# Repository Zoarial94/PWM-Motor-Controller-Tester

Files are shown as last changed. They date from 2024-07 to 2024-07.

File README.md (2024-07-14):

This is a board I designed and put together during my time as a mentor on the FRC team 4467 Titanium Titans. The original purpose of this device was to easily test Falcon 500 Motors since using the CAN interface made it sometimes difficult to troubleshoot. This board ties between a standard FRC battery, and a Falcon 500. A FRC valid circuit breaker is needed to complete the circuit. 

Version 1 of this board failed because I designed the board with one dc-to-dc converter, but ended up having to go with anther due to shortages. The footprint was mirrored on the new chip and it released the magic smoke after recieving 14V on the output side. This version's files are likely lost to time, but was used to make V2.

Version 2 (Currently uploaded) has a slightly smaller circuit board, but is essentially completely the same design. The programming header J2 was changed to the size it was supposed to be (V1 was too small), and U1 was flipped to match the parts I had on-hand. 

In the image below left to right: Version 2 PCB only. Version 1 PCB only. Version 2 with components except a ciruit breaker.
Left to right. Version 2 PCB only. Version 1 PCB only. Version 2 with components except a ciruit breaker.

Unfortunately, I don't believe I ever recorded this working (Although it definitely has). I would have issues handing this to a student to use since everything is so exposed. Software and hardware wise, I think it is fine. (There should maybe be a protection circuit for the 5V side since U1 blew up in version 1 due to the previously mentioned design mistake.)

## Potential improvments. 
* Label the programming pins. (Needs to be reverse engineered again!)
* Use the virtical anderson connector for the battery connection. This allows for an off-the-shelf plastic sleeve to protect the exposed contacts. 
* Design a case. (This could be 3d printed, but with the forces needed to connect the battery, a 3d printed case will need to be designed to withstand large gripping forces.)
* Better protection on the 5V side.

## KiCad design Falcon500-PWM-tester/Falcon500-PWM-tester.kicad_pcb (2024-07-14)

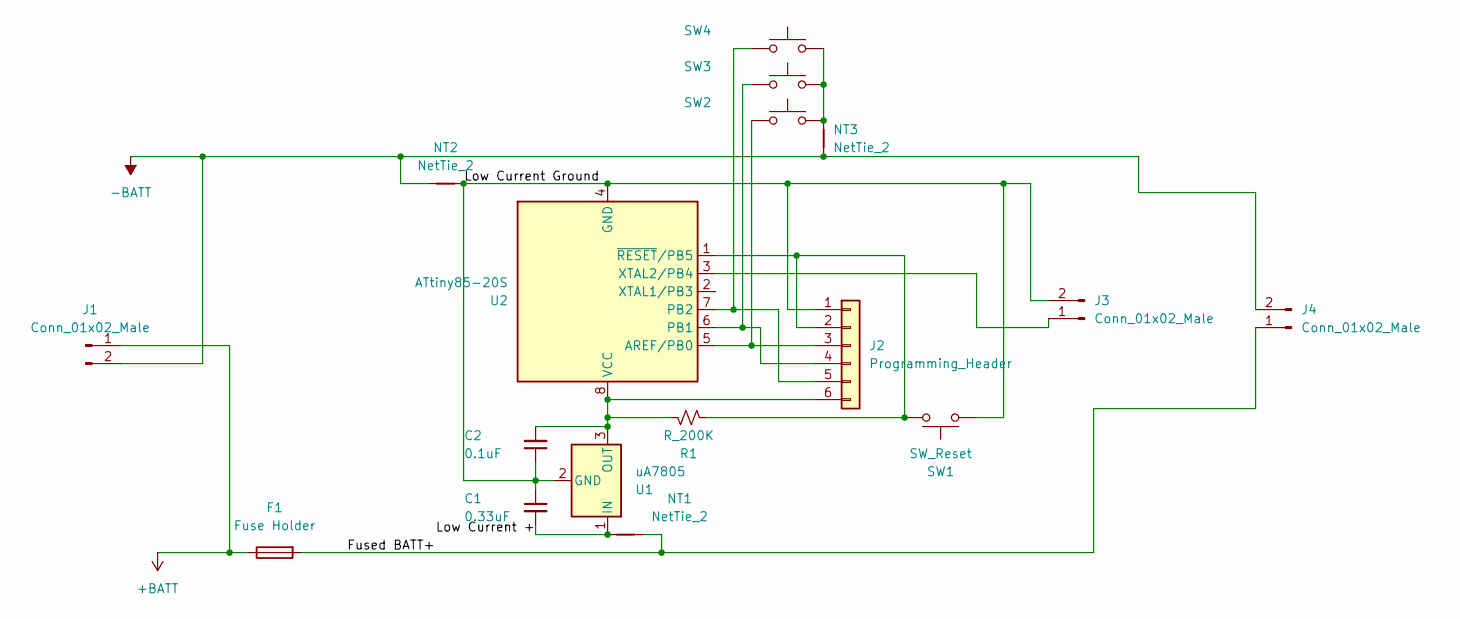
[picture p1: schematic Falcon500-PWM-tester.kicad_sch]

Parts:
C1: 0.33uF; C_0603_1608Metric_Pad1.08x0.95mm_HandSolder
C2: 0.1uF; C_0402_1005Metric_Pad0.74x0.62mm_HandSolder
F1: Fuse Holder; Fuseholder_Littelfuse_Style_ATO_Blade
J1: Conn_01x02_Male; MINI_HORIZONTAL_POWER_CLAW
J2: Programming_Header; PinHeader_1x06_P1.27mm_Vertical
J3: Conn_01x02_Male; TerminalBlock_Phoenix_MKDS-1,5-2-5.08_1x02_P5.08mm_Horizont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
J4: Conn_01x02_Male; PP44_2x1_Horizontal
NT1, NT2, NT3: NetTie_2; NetTie-2_SMD_Pad0.5mm
R1: R_200K; R_Axial_DIN0204_L3.6mm_D1.6mm_P7.62mm_Horizontal
SW1: SW_Reset; SW_PUSH_6mm
SW2: (no value)
SW3, SW4: SW_PUSH_6mm
U1: uA7805; SOT-89-3_Handsoldering
U2: ATtiny85-20S; SOIC-8W_5.3x5.3mm_P1.27mm

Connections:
+BATT: F1.1, J1.1
-BATT: J1.2, J4.2, NT2.1, NT3.1
/Fused BATT+: F1.2, J4.1, NT1.2
/Low Current +: C1.2, NT1.1, U1.1 (IN)
/Low Current Ground: C1.1, C2.1, J2.1, J3.2, NT2.2, SW1.2, U1.2 (GND), U2.4 (GND)
unnamed: C2.2, J2.6, R1.1, U1.3 (OUT), U2.8 (VCC)
unnamed: J2.2, R1.2, SW1.1, U2.1 (~RESET/PB5)
unnamed: J2.3, SW2.1, U2.5 (AREF/PB0)
unnamed: J2.4, SW3.1, U2.6 (PB1)
unnamed: J2.5, SW4.1, U2.7 (PB2)
unnamed: J3.1, U2.3 (XTAL2/PB4)
unnamed: NT3.2, SW2.2, SW3.2, SW4.2

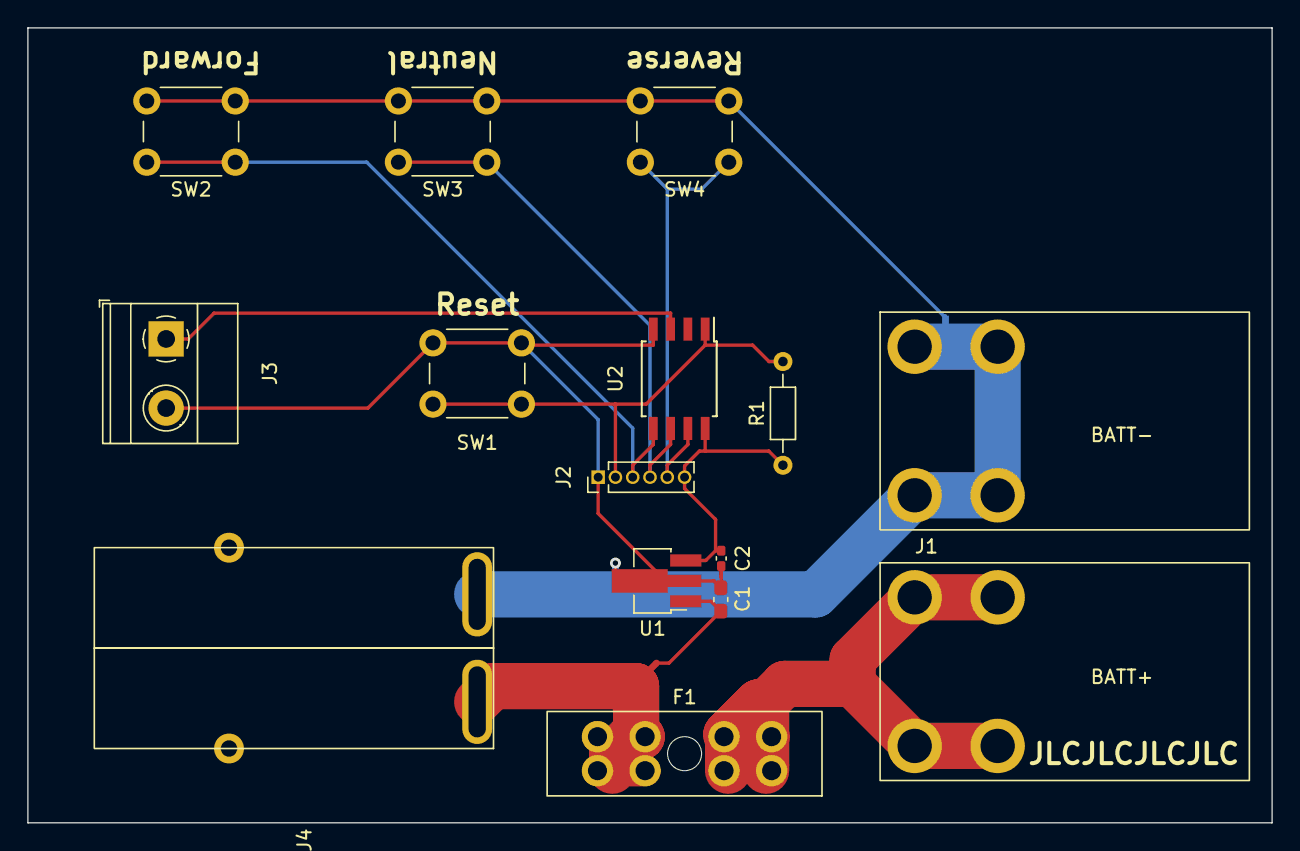
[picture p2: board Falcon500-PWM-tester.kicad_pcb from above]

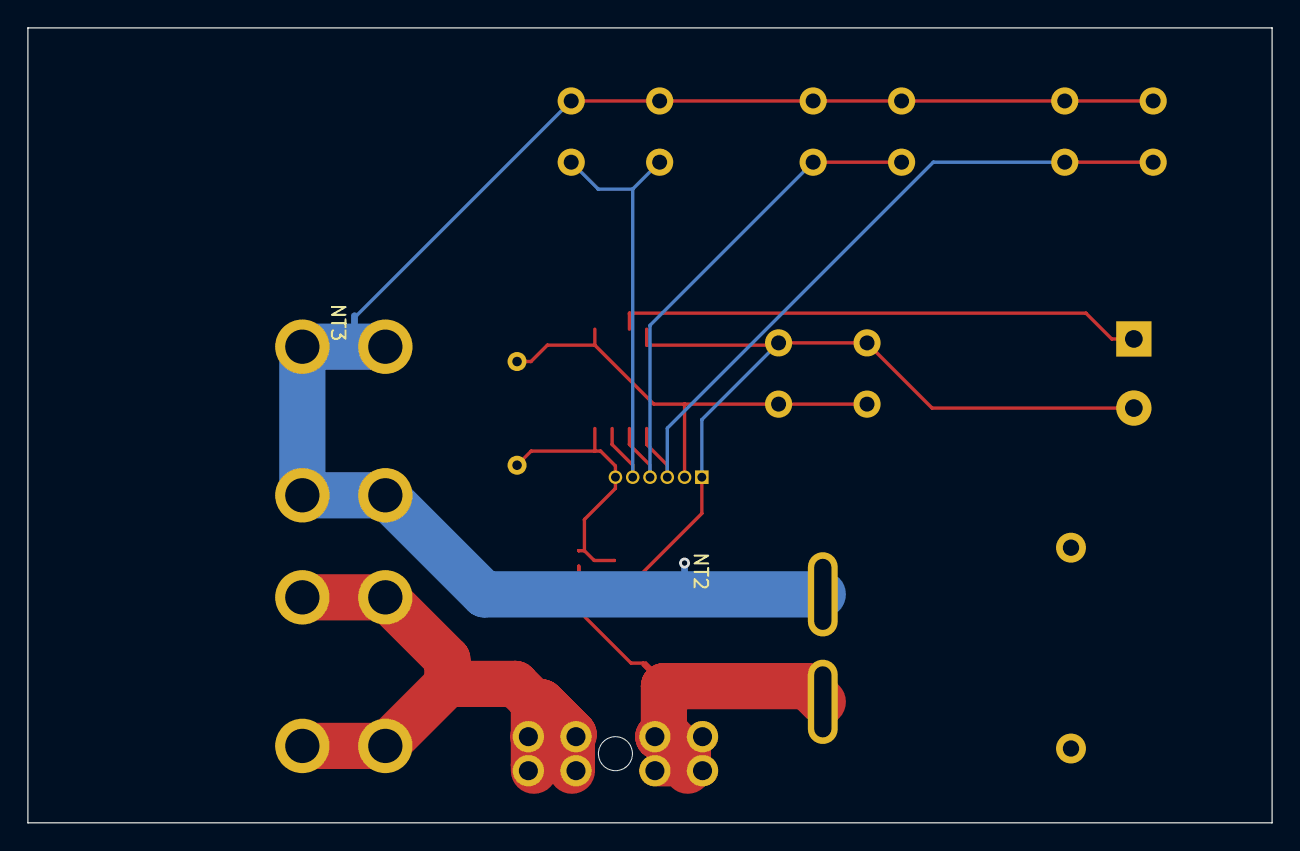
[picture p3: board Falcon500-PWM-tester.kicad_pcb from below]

Board: 2 copper layers, 91.4 x 58.4 mm, 17 parts (2 on the bottom side), 12 nets.

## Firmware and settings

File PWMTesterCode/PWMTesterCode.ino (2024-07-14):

/*
 * 
 * This program was written for the PWM Tester Board. 
 * This code was designed to be flashed onto a ATtiny85
 * 
 * The circuit board is designed to have 3 buttons which pull the input pins to ground
 * There is 1 PWM output for the motor controller
 * 
 */

// Helpers
#define BIT(n) (1<<(n))
#define BITSET(x, n)        ((x) |= bit(n))
#define BITGET(x, n)        (((x) & bit(n)) > 0)



void setup() {
  cli(); // Disable interrupts
  CLKPR = (1<<CLKPCE); // Prescaler enable
  CLKPR = 0x00; // Clock division factor
  sei(); // Enable interrupts

  /* PLL Setup and config
  */
  PLLCSR = (1<<PLLE);
  // Check for PLL Lock insead of just delaying
  delay(10);
  PLLCSR |= (1<<PCKE);

  /* Config Timer 
  *  CTC1 causes the counter to reset at OCR1C counts.
  *  The CS bits select the prescale value. 13, 11, and 10 set the value to 1024
  */
  TCCR1 = (1<<CTC1) | (1<<CS13) | (1<<CS11) | (1<<CS10);

  /* Config Timer (cont.)
  *  PWM1B enables PWM on ouput B
  *  COM1B0 and COM1B1 set output mode
  */
  GTCCR = (1<<PWM1B) | (1<<COM1B0);

/*
 * Setup the main frequency
 * 
 * 250 ticks = 4ms 
 * (64 000 000 / 1024 = 62 500 ticks/sec)
 * (62 500 * 0.004 = 250) 
 * Subtract 1 because hardware reasons
 */
  OCR1C = 250 - 1;

  /*
   * For this motor controller, the input range is 1-2ms. 
   * 1ms is reverse, 1.5ms is neutral, and 2ms is forward. 
   */
  // Set pulse width (94 is ~1.5ms)
  OCR1B = 94;

  // Setup input pins and PWM output
  pinMode(0, INPUT_PULLUP);
  pinMode(1, INPUT_PULLUP);
  pinMode(2, INPUT_PULLUP);
  
  pinMode(4, OUTPUT);
}

/*
 * Constants
 */
const int debounceDelay = 80;

const byte FORWARDBTN = PINB0; 
const byte NEUTRALBTN = PINB1;
const byte REVERSEBTN = PINB2;
const byte NEUTRAL_VALUE = 94;
const byte INC_VALUE = 3;
const byte MAX_RANGE_VALUE = 5;

/* 
 *  Variables
 */

char current_inc = 0;
byte pins[3] = {FORWARDBTN, NEUTRALBTN, REVERSEBTN};
bool lastButtonState[3] = {true};
bool buttonState[3] = {true};
int lastDebounceTime[3] = {0};

// Main loop. Loops over each button one at a time
void loop() {


  /*
   * Read the state of the current button, debounce, check to see if a button is pressed, and then act accordingly
   */
  for(int i = 0; i < 3; i++) {
    bool reading = BITGET(PINB, pins[i]);

    // If the switch changed due to noise or pressing, then reset the debouncing timer
    if (reading != lastButtonState[i]) {
      lastDebounceTime[i] = millis();
    }

    if ((millis() - lastDebounceTime[i]) > debounceDelay) {
      // Whatever the reading is at, it's been there for longer than the debounce
      // It is safe to take action

      // Check if the button state has changed
      if (reading != buttonState[i]) {
        buttonState[i] = reading;

        // Only change the PWM output if the physical button is pressed (Pin is pulled low)
        if (buttonState[i] == 0) {
          switch(pins[i]) {
            case FORWARDBTN:
              if(current_inc < MAX_RANGE_VALUE) { // Bound check
                current_inc++;
              }
              break;
            case NEUTRALBTN:
              current_inc = 0;
              break;
            case REVERSEBTN:
              if(current_inc > -MAX_RANGE_VALUE) { // Bound Check
                current_inc--;
              }
              break;
          }
          OCR1B = NEUTRAL_VALUE + current_inc * INC_VALUE; // Recalculate the PWM value
        }
      }// If the button is pressed
    } // If debounce passes

    // Setup for the next loop
    lastButtonState[i] = reading;
  } // For(...) each button
} // loop()
